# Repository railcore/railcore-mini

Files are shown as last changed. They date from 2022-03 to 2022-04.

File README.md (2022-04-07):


# RailCore® Mini
The RailCore® Mini is a CoreXY-based RepRap 3D printer designed by J. Steve White and Tony Akens and published under the CC Attribution International license.

<p align="center">
  
</p>

## Overview
The frame is designed to use 1515 aluminum extrusions. This was a space-efficient choice, which makes building the printer easier, as standard M3 hardware fits nicely into the extrusion like T-Nuts would. To add rigidity, we use sides made from Acrylic or HDPE to stiffen the frame. These can alternatively be cut out of any material you prefer, including melamine, plywood and aluminum.

Notable aspects of the design include:

- 3 trapezoidal lead screw Z-axis, stacked idlers, and duo-planar belt path
- The electronics in the design are the Duet 3 Mini 5+, Duet 3 Expansion Mini 2+, Options Raspberry Pi, 24v PSU and 0.9 degree steppers.
- We use an E3D Revo Micro for the design, as it’s the lightest avaliable at this time.
- Support for other hotends such as E3D Revo 6, V6, Volcano, Slice Mosquito, and many others are also available.
- Semi-direct drive or full bowden are both supported

## Build of Materials
The BOM is hosted on [Google Sheets](https://docs.google.com/spreadsheets/d/1TM1vca-hA29apzcBjQ2FyvvZ5D19cWTZl7NxzBflSlU).

## Build Documentation

Documentation for building your own RailCore® Mini can be found on [railcore.dozuki.com](https://railcore.dozuki.com/c/RailCore%C2%AE_Mini_Kit). If you need assistance with your build, a strong community of support is available on our Discord server.

Discord Shield (https://discord.gg/w2ccNBMC)

**A special thanks to Filastruder, Duet3d, E3D, 713Maker, and Mandala Roseworks for supporting the project.**

Thanks to Project R3d for components donated in the early beta process of the RailCore Mini.

*RailCore® is a registered trademark of RailCore Labs, LLC.*

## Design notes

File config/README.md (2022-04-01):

# Duet Configurations
The provided configuration files should be placed in the `/sys` folder of the Duet SD card.

*RailCore® is a registered trademark of RailCore Labs, LLC.*

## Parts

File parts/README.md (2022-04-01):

# Parts
In this folder you will find both source files and printable parts specific to the RailCore® Mini.

Notable source files you won't find here are shared with the 300 ZL/ZLT and can be found [here](https://github.com/railcore/parts/tree/master/STEP).

- Motor Mounts
- Pully Mounts
- X Carriages

## Panels
Drawings of the 5 panels are available in the `DXF/` folder if you would like to cut your own. The recommended material and thickness is 6mm acrylic or polycarbonate.

## Printed Parts
Notable `STL` files you won't find here are shared with the 300 ZL/ZLT.

- [Idler Spacers](https://github.com/railcore/parts/blob/master/STL/Idler_Spacer.stl) (Not required for inboard Magnum idlers/mounts)
- [Belt Retainer Clips](https://github.com/railcore/parts/blob/master/STL/Belt_Retainer_Clip.stl)
- [Y Endstop Mount](https://github.com/railcore/parts/blob/master/STL/Y_Endstop_Mount.stl)
- [BLTouch Mount](https://github.com/railcore/parts/blob/master/STL/BLTouch_Mount.stl)
- [James Tongue Fan Duct](https://github.com/railcore/parts/blob/master/STL/cooling_shroud_hangtight_james_tongue/Duct_Printed_Mount_V2.stl)
- [Printed Fan Mount Adapter](https://github.com/railcore/parts/blob/master/STL/cooling_shroud_hangtight_james_tongue/Duct_Printed_Mount_Adapter.stl) (Not compatible with aluminum carriage)

#### Hotend Mounts
Printed hotend mounts from the 300ZL will fit the RailCore® Mini Y carriage and can be found [here](https://github.com/railcore/parts/tree/master/STL/hotend_groove_mounts).

*RailCore® is a registered trademark of RailCore Labs, LLC.*

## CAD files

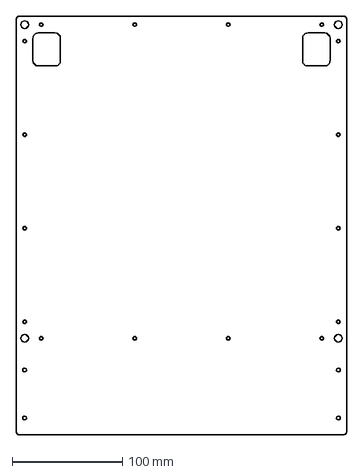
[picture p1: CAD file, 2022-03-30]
parts/DXF/right-panel.dxf
300.0 x 380.0 mm

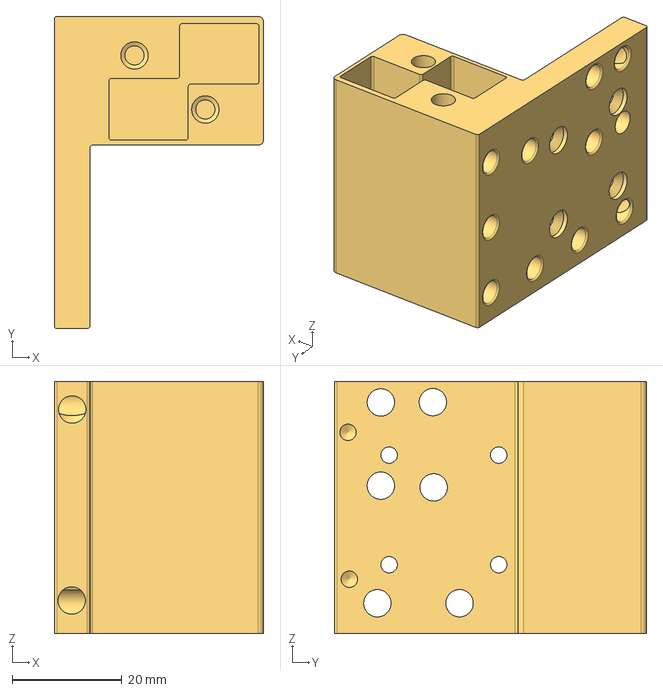
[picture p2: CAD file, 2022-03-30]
parts/STEP/y-carriage.step
38.2 x 57.0 x 46.0 mm

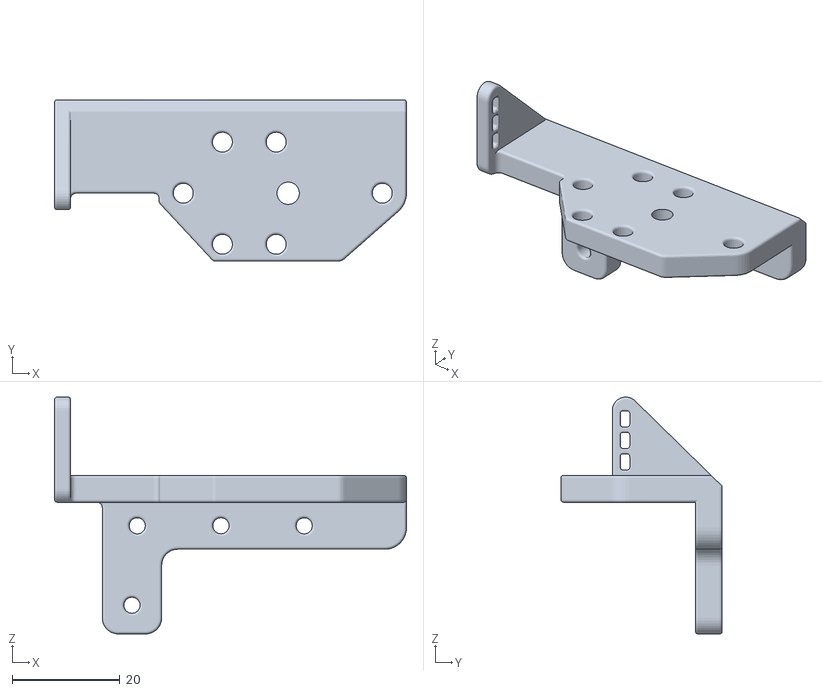
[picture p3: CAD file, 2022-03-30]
parts/STL/lgx-orbiter-combo-mount.stl
65.4 x 30.0 x 44.1

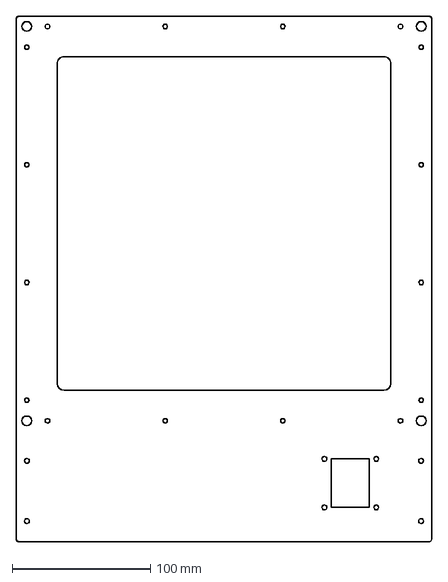
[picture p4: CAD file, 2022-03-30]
parts/DXF/front-panel.dxf
300.0 x 380.0 mm

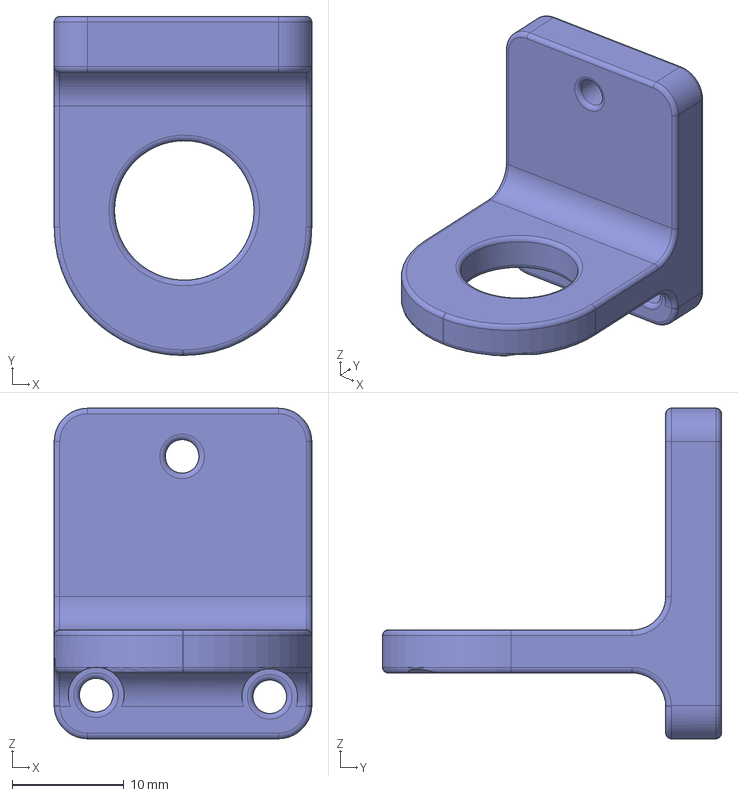
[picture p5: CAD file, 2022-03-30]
parts/STEP/revo-micro-mount.step
23.1 x 30.4 x 29.6 mm

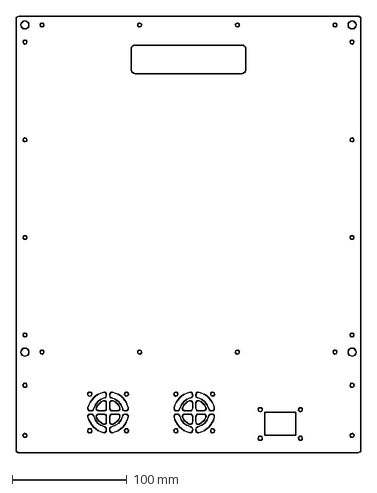
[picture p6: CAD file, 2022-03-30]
parts/DXF/back-panel.dxf
300.0 x 380.0 mm

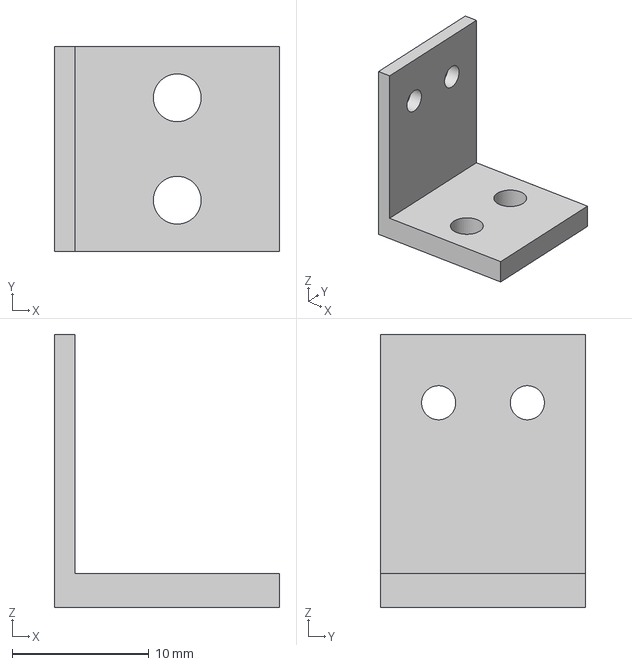
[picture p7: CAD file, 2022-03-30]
parts/STEP/x-endstop.step
16.5 x 15.0 x 20.0 mm

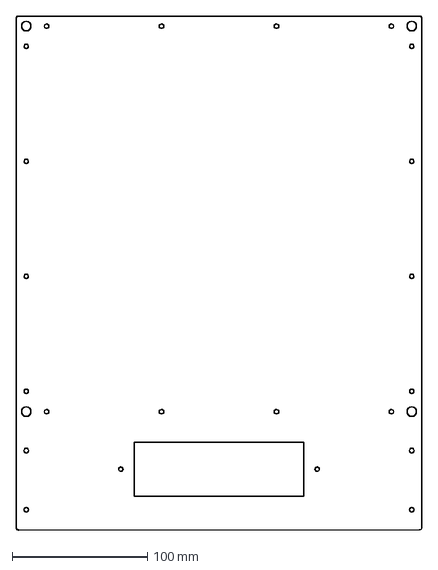
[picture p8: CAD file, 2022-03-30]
parts/DXF/left-panel.dxf
300.0 x 380.0 mm

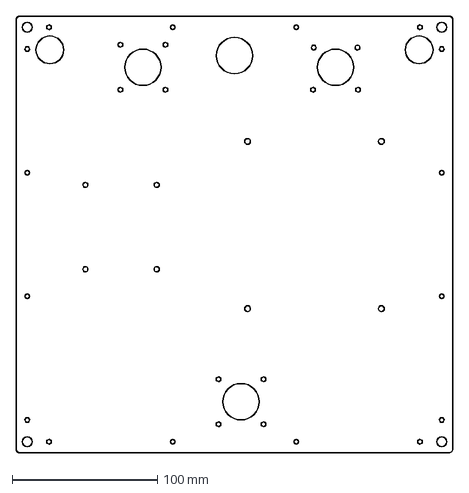
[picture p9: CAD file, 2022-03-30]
parts/DXF/botom-panel.dxf
300.0 x 300.0 mm

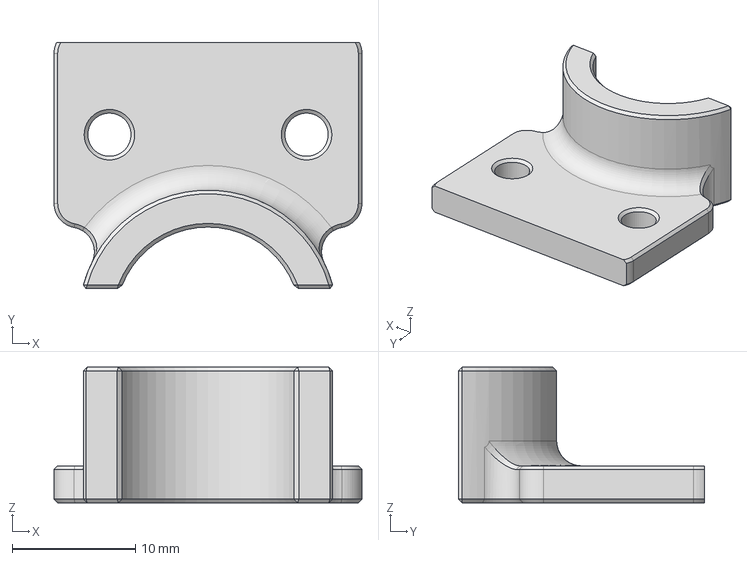
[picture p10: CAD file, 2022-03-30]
parts/STEP/wire-loom.step
25.0 x 20.0 x 11.0 mm

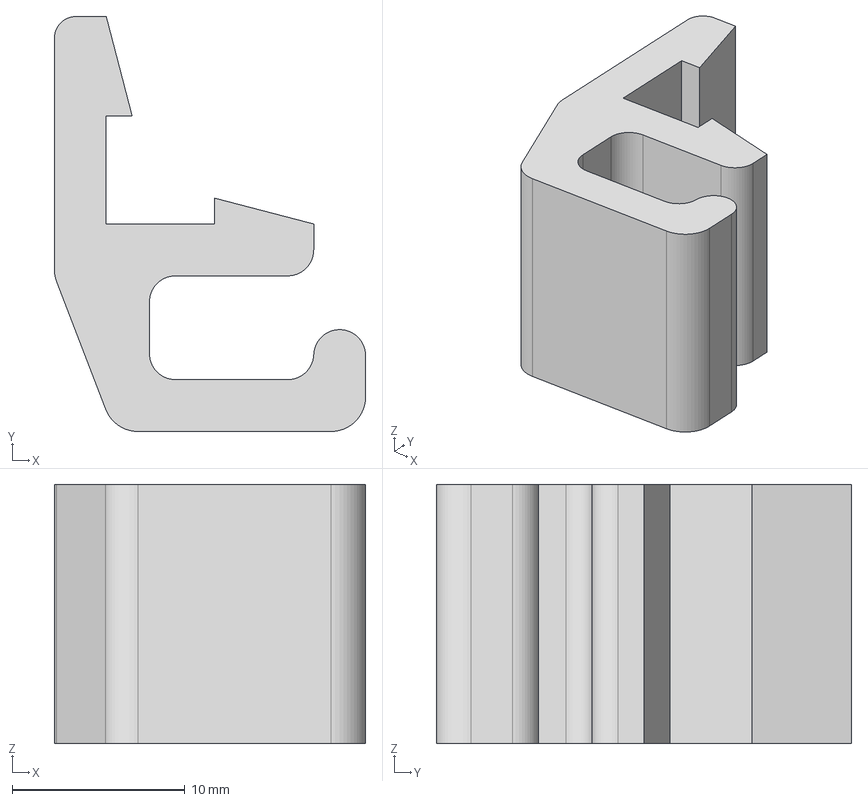
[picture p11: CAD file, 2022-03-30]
parts/STEP/wire-clip.step
18.0 x 24.0 x 15.0 mm

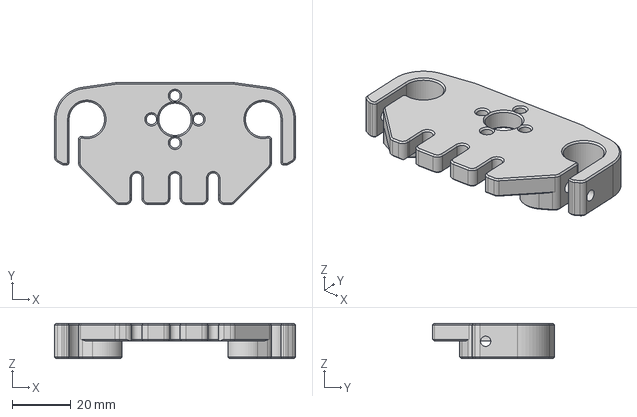
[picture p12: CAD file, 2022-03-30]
parts/STEP/z-tower-slide.step
82.0 x 41.4 x 12.0 mm

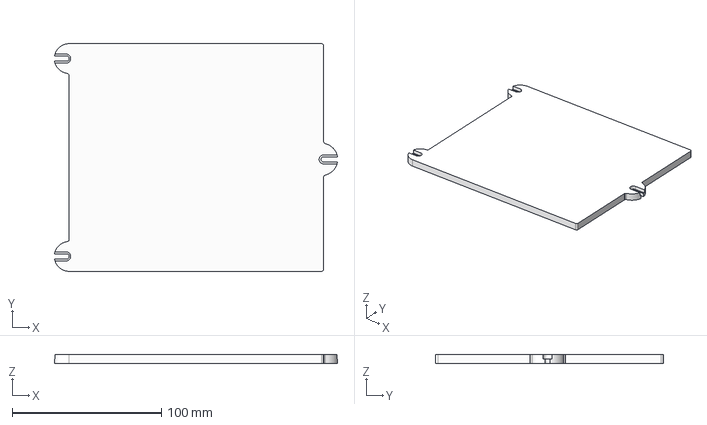
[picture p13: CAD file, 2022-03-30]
parts/STEP/bed.step
189.5 x 152.5 x 6.00 mm

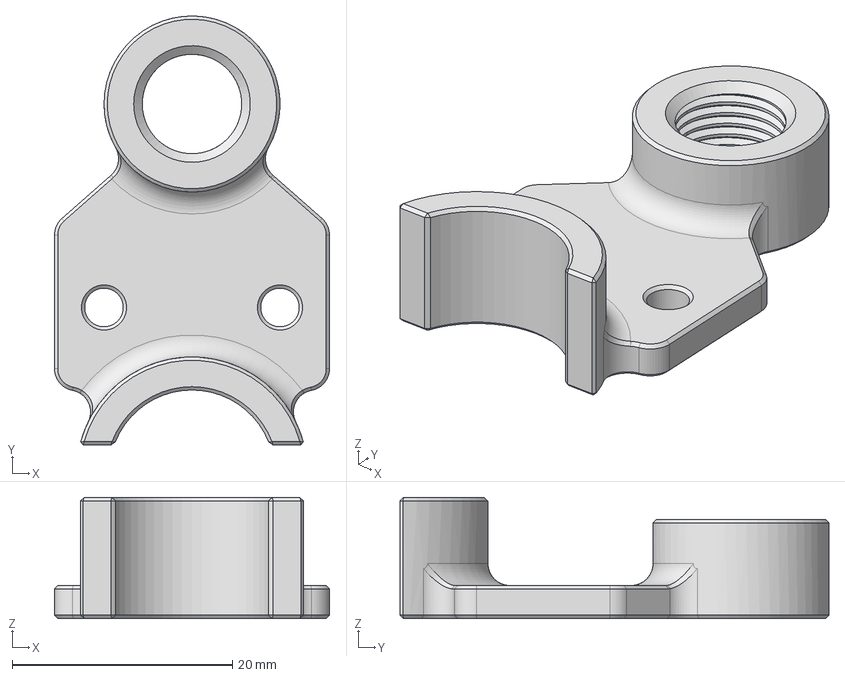
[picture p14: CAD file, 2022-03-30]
parts/STEP/wire-loom-ptfe-retainer.step
25.0 x 39.0 x 11.0 mm

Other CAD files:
parts/STEP/lgx-lite-orbiter-combo-mount.step
parts/STEP/rod-carrier.step
parts/STEP/power-switch.step
parts/STEP/power-inlet.step
parts/STEP/foot.step
parts/STEP/usb-wifi-inlet.step
parts/STL/foot.stl
parts/STL/power-inlet.stl
parts/STL/power-switch.stl
parts/STL/revo-micro-mount.stl
parts/STL/usb-wifi-inlet.stl
parts/STL/wire-clip.stl
parts/STL/wire-loom-ptfe-retainer.stl
parts/STL/wire-loom.stl
parts/STL/x-endstop.stl
parts/STL/y-carriage.stl
parts/STL/z-tower-slide.stl

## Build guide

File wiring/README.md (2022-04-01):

# Wiring
The provided `YAML` files for the RailCore® Mini wiring were created with [WireViz](https://github.com/formatc1702/WireViz).

## Bed Heater Harness
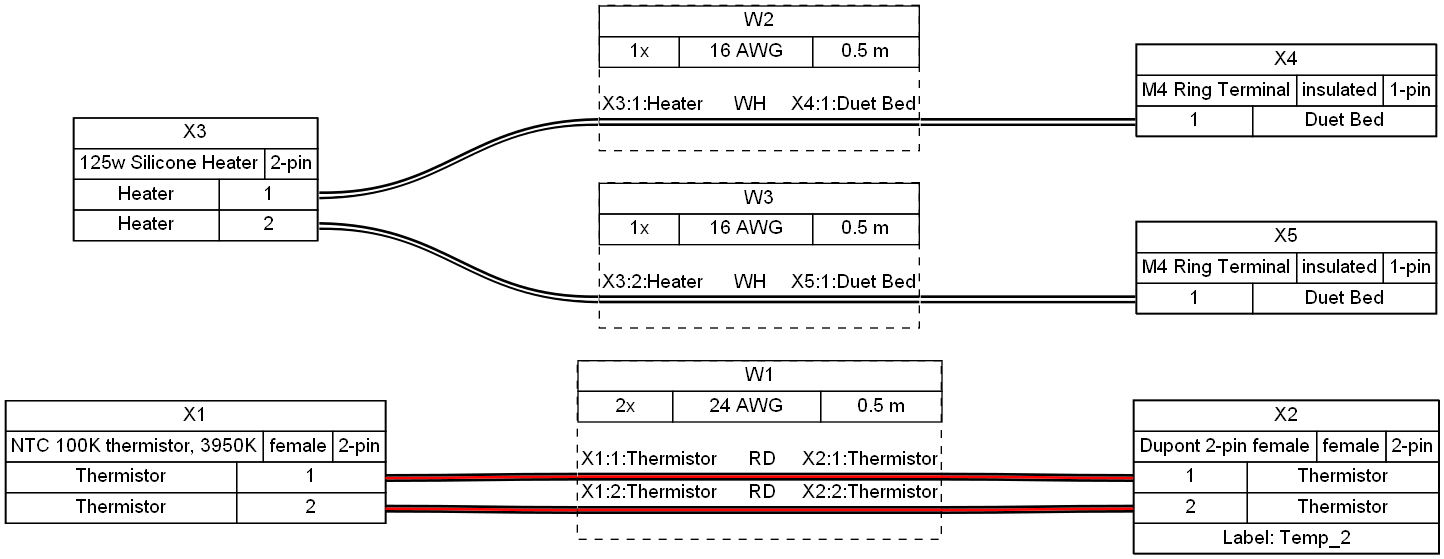
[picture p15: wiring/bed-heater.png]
Bed


## Main Harness
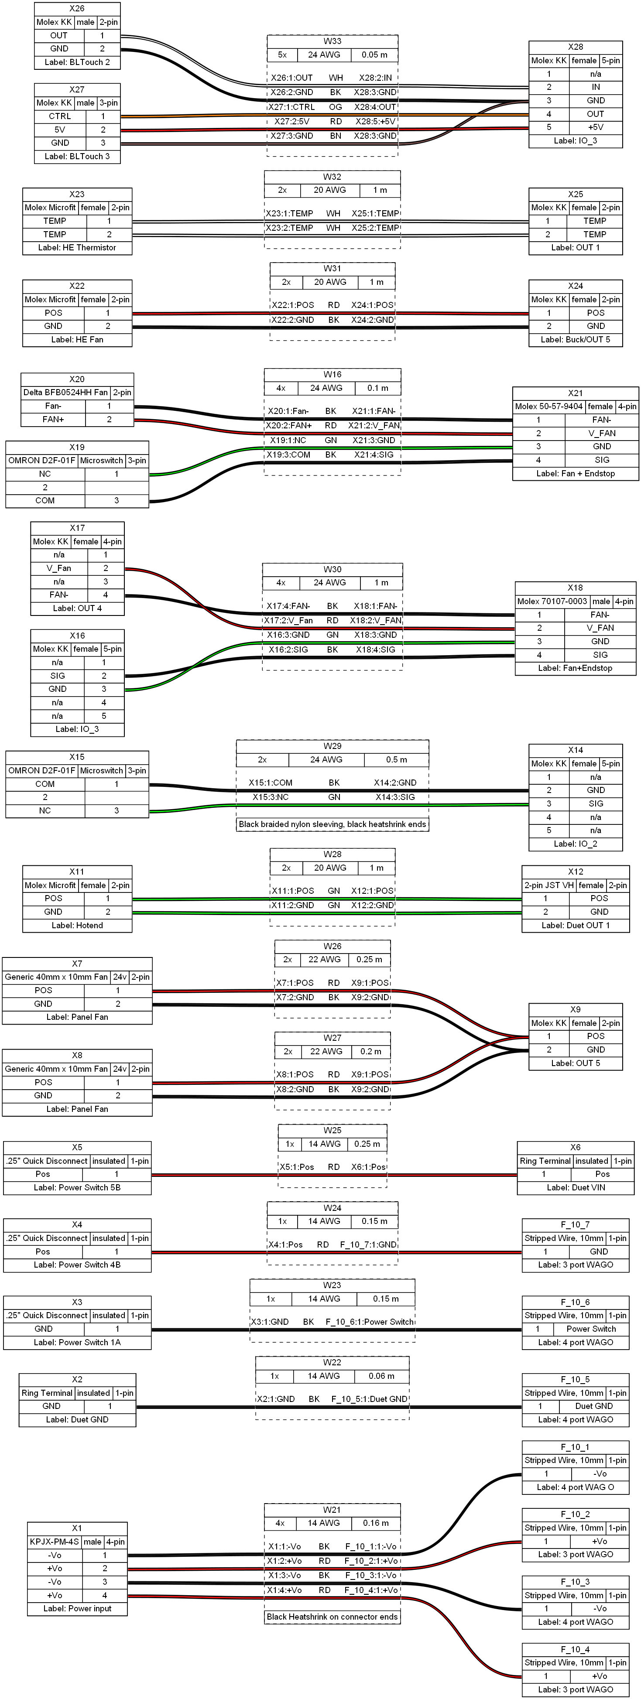
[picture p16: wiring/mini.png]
Harness


*RailCore® is a registered trademark of RailCore Labs, LLC.*

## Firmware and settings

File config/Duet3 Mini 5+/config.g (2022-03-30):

; RailCore Mini Duet3 Mini 5+ Configuration
; config.g

G21						;Work in millimetres
G90						;Send absolute coordinates...
M83						;...but relative extruder moves

M550 P"RailCoreMini"

;Wifi Networking
M552 S1								; Enable WiFi

M575 P1 S1 B57600

;Axis and motor configuration
M569 P0 S0 D3					;Drive 0 Extruder
M569 P1 S1 D3					;Drive1 Unused
M569 P2 S0 D3					;Drive 2 Z Front Right
M569 P3 S0 D3					;Drive 3 Z Rear Right
M569 P4 S0 D3					;Drive 4 Z Left
M569 P5 S1 D3					;Drive 5 Y / Front
M569 P6 S0 D3					;Drive 6 X / Rear
M667 S1						    ;corexy mode

M584 X6 Y5 Z4:3:2 E0	;Map X to drive 6 Y to drive 5 Z to drives 2, 3, 4, and E to drive 0

;Leadscrew locations
M671 X-5:165:165  Y90:155:22.5 S7.5		;X -10, -10, 315

M350 X16 Y16 Z16 E16 I1				      ;Set 16x microstepping for axes with interpolation
M906 X1400 Y1400 Z1200 E800 I80			;Set motor currents (mA)
M201 X2000 Y2000 Z150 E1500			    ;Accelerations (mm/s^2)
M204 P1400 T4000
M203 X12000 Y12000 Z900 E3600			  ;Maximum speeds (mm/min) was Z1800 tr8*4
M566 X1000 Y1000 Z150 E1800			    ;Maximum jerk speeds mm/minute E60 Z60
M208 X150 Y150 Z150				          ;Set axis maxima and high homing switch positions (adjust to suit your machine)
M208 X0 Y0 Z0 S1				            ;Set axis minima and low homing switch positions (adjust to make X=0 and Y=0 the edges of the bed)
M92 X200 Y200 Z1600 E562            ;Steps/mm

; End Stops
M574 X2 S1 P"io2.in"				        ;Map the X endstop to io2.in
M574 Y1 S1 P"io4.in"				        ;Map the Y endstop to io4.in

; Thermistors
M308 S0 P"temp0" Y"thermistor" A"bed_heat" T100000 B4240 H0 L0 		      ;Bed thermistor
M308 S1 P"temp1" Y"thermistor" A"e0_heat" T100000 B4725 C7.06e-8 H0 L0	;E3D Revo thermistor

;Define Heaters
M950 H0 C"out0" T0				;Bed heater is on out0
M950 H1 C"out1" T1				;Hotend heater is on out1

;Define Bed
M140 H0

M570 S360					;Hot end may be a little slow to heat up so allow it 180 seconds
M143 S285					;Set max hotend temperature

; Fans
M950 F1 C"out4"					;Layer fan on "out4" connector
M106 P1 S0 						  ;Layer fan default speed
M950 F2 C"out5"					;Case fans on "out5" connector
M106 P2 S255 					  ;Case fans default speed
M950 F3 C"out6"         ;Hotend fan on "out6" connector
M106 P3 S255 H1 T50 		;Enable thermostatic mode for hotend fan

; Tool definitions
M563 P0 D0 H1 F1        ;Define tool 0
G10 P0 S0 R0            ;Set tool 0 operating and standby temperatures

;BLTouch
M558 P9 C"io3.in" H5 R1 F120 T6000 A5 S0.02 B1	;define the bltouch input on io3.in
M950 S0 C"io3.out"					                    ;define the bltouch servo on io4.out
G31 X2 Y42 Z1.843 P25				                    ;set the offsets for the bltouch

T0 ;select first hot end

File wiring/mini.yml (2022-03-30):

connectors:
  X1:
    type: KPJX-PM-4S
    subtype: male
    pinlabels: [-Vo, +Vo, -Vo, +Vo]
    notes: "Label: Power input"

  F_10_1: # manually define a ferrule (with unique designator)
    pinlabels: [-Vo]
    category: ferrule
    type: Stripped Wire, 10mm
    notes: "Label: 4 port WAG
    O"
  F_10_2: # manually define a ferrule (with unique designator)
    pinlabels: [+Vo]
    category: ferrule
    type: Stripped Wire, 10mm
    notes: "Label: 3 port WAGO"

  F_10_3: # manually define a ferrule (with unique designator)
    pinlabels: [-Vo]
    category: ferrule
    type: Stripped Wire, 10mm
    notes: "Label: 4 port WAGO"

  F_10_4: # manually define a ferrule (with unique designator)
    pinlabels: [+Vo]
    category: ferrule
    type: Stripped Wire, 10mm
    notes: "Label: 3 port WAGO"

  X2:
    pinlabels: [GND]
    type: Ring Terminal
    subtype: insulated
    notes: "Label: Duet GND"

  F_10_5: # manually define a ferrule (with unique designator)
    pinlabels: [Duet GND]
    category: ferrule
    type: Stripped Wire, 10mm
    notes: "Label: 4 port WAGO"

  X3:
    pinlabels: [GND]
    type: .25" Quick Disconnect
    subtype: insulated
    notes: "Label: Power Switch 1A"

  F_10_6: # manually define a ferrule (with unique designator)
    pinlabels: [Power Switch]
    category: ferrule
    type: Stripped Wire, 10mm
    notes: "Label: 4 port WAGO"

  X4:
    pinlabels: [Pos]
    type: .25" Quick Disconnect
    subtype: insulated
    notes: "Label: Power Switch 4B"

  F_10_7: # manually define a ferrule (with unique designator)
    pinlabels: [GND]
    category: ferrule
    type: Stripped Wire, 10mm
    notes: "Label: 3 port WAGO"

  X5:
    pinlabels: [Pos]
    type: .25" Quick Disconnect
    subtype: insulated
    notes: "Label: Power Switch 5B"

  X6:
    pinlabels: [Pos]
    type: Ring Terminal
    subtype: insulated
    notes: "Label: Duet VIN"

  X7:
    pinlabels: [POS, GND]
    type: Generic 40mm x 10mm Fan
    subtype: 24v
    notes: "Label: Panel Fan"

  X8:
    pinlabels: [POS, GND]
    type: Generic 40mm x 10mm Fan
    subtype: 24v
    notes: "Label: Panel Fan"

  X9:
    pinlabels: [POS, GND]
    type: Molex KK
    subtype: female
    notes: "Label: OUT 5"

  X11:
    pinlabels: [POS, GND]
    type: Molex Microfit
    subtype: female
    notes: "Label: Hotend"

  X12:
    pinlabels: [POS, GND]
    type: 2-pin JST VH
    subtype: female
    notes: "Label: Duet OUT 1"

  X14:
    type: Molex KK
    subtype: female
    pinlabels: [n/a, GND, SIG, n/a, n/a]
    notes: "Label: IO_2"

  X15:
    pinlabels: [COM, NO, NC]
    type: OMRON D2F-01F
    subtype: Microswitch

  X16:
    type: Molex KK
    subtype: female
    pinlabels: [n/a, SIG, GND, n/a, n/a]
    notes: "Label: IO_3"

  X17:
    type: Molex KK
    subtype: female
    pinlabels: [n/a, V_Fan, n/a, FAN-]
    notes: "Label: OUT 4"

  X18:
    type: Molex 70107-0003
    subtype: male
    pinlabels: [FAN-, V_FAN, GND, SIG]
    notes: "Label: Fan+Endstop"

  X19:
    pinlabels: [NC, NO, COM]
    type: OMRON D2F-01F
    subtype: Microswitch

  X20:
    type: Delta BFB0524HH Fan
    pinlabels: [Fan-, FAN+]

  X21:
    type: Molex 50-57-9404
    subtype: female
    pinlabels: [FAN-, V_FAN, GND, SIG]
    notes: "Label: Fan + Endstop"

  X22:
    pinlabels: [POS, GND]
    type: Molex Microfit
    subtype: female
    notes: "Label: HE Fan"

  X23:
    pinlabels: [TEMP, TEMP]
    type: Molex Microfit
    subtype: female
    notes: "Label: HE Thermistor"

  X24:
    pinlabels: [POS, GND]
    type: Molex KK
    subtype: female
    notes: "Label: Buck/OUT 5"

  X25:
    pinlabels: [TEMP, TEMP]
    type: Molex KK
    subtype: female
    notes: "Label: OUT 1"

  X26:
    pinlabels: [OUT, GND]
    type: Molex KK
    subtype: male
    notes: "Label: BLTouch 2"

  X27:
    pinlabels: [CTRL, 5V, GND]
    type: Molex KK
    subtype: male
    notes: "Label: BLTouch 3"

  X28:
    type: Molex KK
    subtype: female
    pinlabels: [n/a, IN, GND, OUT, +5V]
    notes: "Label: IO_3"
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

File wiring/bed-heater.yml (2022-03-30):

connectors:
  X1:
    type: NTC 100K thermistor, 3950K
    subtype: female
    pinlabels: [Thermistor, Thermistor]
  X2:
    type: Dupont 2-pin female
    subtype: female
    pinlabels: [Thermistor, Thermistor]
    notes: "Label: Temp_2"


  X3:
    type: 125w Silicone Heater
    pinlabels: [Heater, Heater]

  X4:
    pinlabels: [Duet Bed]
    type: M4 Ring Terminal
    subtype: insulated

  X5:
    pinlabels: [Duet Bed]
    type: M4 Ring Terminal
    subtype: insulated


cables:
  W1:
    category: bundle # bundle
    length: 0.5
    gauge: 24 AWG
    colors: [RD, RD] # custom colors, wirecount is implicit
  W2:
    category: bundle # bundle
    length: 0.5
    gauge: 16 AWG
    colors: [WH] # custom colors, wirecount is implicit
  W3:
    category: bundle # bundle
    length: 0.5
    gauge: 16 AWG
    colors: [WH] # custom colors, wirecount is implicit


connections:
  - # attach ferrules
    - X1: [1,2]
    - W1: [1,2]
    - X2: [1,2]

  - # attach ferrules
    - X3: [1]
    - W2: [1]
    - X4: 1
  - # attach ferrules
    - X3: [2]
    - W3: [1]
    - X5: [1]

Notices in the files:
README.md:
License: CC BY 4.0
